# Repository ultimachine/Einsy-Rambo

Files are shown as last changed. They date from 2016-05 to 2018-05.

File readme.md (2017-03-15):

Mini-Rambo

3D Printer controller.

This board is based of RAMBo based off the Arduino MEGA design and work of RepRap community. It has 4 stepper drivers and 4 mosfet switched outputs.

There is no warantee for these files in any way. There may have been some undocumented tweaks by various designers, engineers, manufacturers, suppliers, and assemblers to make this a functional product.

#Version History
Note: This design was previously known as "Mini-RAMBo"  Previous versions of this design can be found at https://github.com/ultimachine/Mini-Rambo

v0.3a:
- Changed name from "Mini-Rambo" to "Einsy-Rambo".
- Uses the Trinamics TMC2130 motor driver in a 5x6mm QFN36 package.
- Added series resistance and TVS to selected signals.
- Overvoltage protection added to thermistors.
- Corrected and added testpoints
- Added GPIO connection "XTRA0" (currently unused) from 32U2, through the galvanic isolator, and into the Mega2560
- Added ferrite to AVdd pin of the 32U2
- Moved the XTAL of the 32U2
- Fixed the soldermask under the 5V buck regulator
- Removed via tenting underneath QFN packages, as well as all other packages with an SMT heat slug/tab
- Added pin1 marking to silkscreen
- Added teardrops to vias
- Changed via sizes to 10/22 and 15/30 (mils).
- Added GND polygon to XTAL of Mega2560
- Changes 5V inductor footprint for the 5V buck converter to fit two differing inductor package mechanicals
- Added I2C pullups (currently set to "Do Not Stuff")
- Adjustments to fuse holder footprint
- Decreased t-hole size of main power connector
- Fan connectors now have a third pin for reading fan tach pulses.
- Adjusted stackup to be more "standard"
- Added 100R to the gate of each FET

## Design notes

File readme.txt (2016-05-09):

Mini-Rambo readme

Part Changes
C40 0402 > 0603
C25 0603 > 0402
C49 0603 > 0402, 10nf > 1uF
F5 1210 > 1812
C1 0603 > 0402
C16 0603 > 0402

C30 change part to C1206C475K5PACTU - same values, worse tolerance, better supply chain, better price

Temporary use WSL2010R0600FEA18 for sense resistor on smps
Change R13 sense resistor to RL2512FK-070R06L

Proposed part changes
56R > 0R > REMOVED
0R > REMOVED

Extension connectors

Tasks
 Firmware
  Pins
  motor current by PWM
  
0.1 errata
PS_ON not connected 
LEDs placed 180 out
atmega2560, A4982 placed 270 out
PSMN70 placed offset in Y
USB fuse too close to USB connector. Remove?
No ESD path for USB, TVS diode added to bottom
No polarity indicator on connectors

0.2 errata
fuse holder hole too small, verify hole size is as spec'd
stencil sucks
No ESD path for USB, TVS diode added to bottom
 
Tests - Start up, Steady state, Transient states
EM
 voltage regulator
 motors
Temperatures
 Bed Fet
  V= 11 - 25, A= 15+
 Extruder Fet
  V= 11 - 25, A= 5+
 Fan Fets
 Motor Drivers
 Power traces
 Voltage regulator
ESD
 USB
Voltage
 Reverse voltage Input
 Min/Max voltage

Induced noise / interference
 ADC
 SMPS onto other lines
 
Stepper current circuit
 700mV P-P, ~40ns period. Saved #1 

Concerns
Fan connector selection.
Must be actively cooled.
motor output filters removed. necessity will need to be evalutated again for new design
see errata for individual versions above

Silk screen on QFN32
icsp typo

power from 5vsb leaves on with power off - jumper select

Fuse hole size

ATX testpoints 

clock too close to buzzer?

Change to smt connector? CNC tech has no button?

is clamping diode on motor power rail?

more pins broke out!!? 5v,tx,rx,gnd,reset  , i2c

tighten smps to allow shield

SMT extension headers? 

Shrink annular ring on usb 2x4

ATX
trace on D10 out jack

clean up polygons (bed)+
traces
silk screens

qfn and fets
no tent on vias
thermal pad print too small

ATX no option to force psu on with vcc set to 5V rail

1.0a //////////////////////////////////////////////////////////////////

add tp for vref & ? on top
xy e ref pins switched in firmware
label testpoints, bottom silk

1.1a////////////////////////////////////////////////
tent mosfet vias

1.3a errata
"Therm" silk screen too far right
T2 silk too far right.
via in F3 pads top right and bottom left
fuse hole size?

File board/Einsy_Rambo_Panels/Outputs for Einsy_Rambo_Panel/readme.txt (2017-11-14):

Readme File for Printed Circuit Board 'Einsy_Rambo_1.1a'

Board Specification
Part Number            Einsy_Rambo
Revision               1.1a
Board size             105 x 71mm
Board Thickness        1.524mm (0.06")
Board type             Rigid
Number of layers       6
P.C.B material         RoHS TG170
Finished Copper        2oz, 1oz (See Stackup)
Finish                 ENIG (Gold) (Lead free) (RoHS)
Mask type              See special requirement below
Mask color             Orange -See special requirement below
Silk screen color      Black -See special requirement below
Silk screen Sides      BOTH 
Min trace width        0.006"
Min clearance          0.008"
Min Hole Diameter >=   10mil
Gold Edge Connectors   No
Internal slots/routes  0
Blind Vias             No
Buried Vias            No
No of Boards/Panel     3
Routing                V-Score
Panel Size     116.8 X 226.1mm

Drill format           Leading zero suppression 2.4

Special Requirements
1. Fabricate PCB in accordiance with IPC-A-600 CLASS 2 (LATEST REVISION)
2. The PCB must be lead free assembly process compatible.
  Must handle minimum 6 cycles - 260C for 10 seconds.
3. Please ship panels including rails with tooling holes and fiducials in gerber files.
4.UL LOGO + ID and ROHS logo to be placed on solder side (bottom silk screen) by board fab in regions .
5. We wish to have an orange soldermask with a black soldermask on top. Print soldermask Orange as 
  provided. Print silk screen layer Einsy_Rambo_Panel.GTO INVERTED (negative) in black.
  The end result should be a black surface with orange silkscreen legend showing from beneath. 
  See image Black-Orange.png
6. Please note that extra top silkscreen has been poured around several QFN packages.
  Please do not remove this silkscreen... the silkscreen fixes an anomaly where black
  and orange soldermask stack up and raise the QFN package off of the land pattern.
  Placing the extra silckscreen causes the black soldermask to be removed in these areas,
  which fixes the problem.

Critical Tolerances: None

Layer Description
(Note: Inner layers are counted from the top downwards)
Top Paste                     Einsy_Rambo_Panel.GTP
Top Silk Screen               Einsy_Rambo_Panel.GTO
Top Solder Mask               Einsy_Rambo_Panel.GTS
Top Copper                    Einsy_Rambo_Panel.GTL
Inner Plane 1                 Einsy_Rambo_Panel.GP1
Inner Signal 1                Einsy_Rambo_Panel.G1
Inner Signal 2                Einsy_Rambo_Panel.G2
Inner Signal 3                Einsy_Rambo_Panel.G3
Bottom Copper                 Einsy_Rambo_Panel.GBL
Bottom Solder Mask            Einsy_Rambo_Panel.GBS
Bottom Silk Screen            Einsy_Rambo_Panel.GBO
NC Drill File                 Einsy_Rambo_Panel.TXT
Board Dimensions              Einsy_Rambo_Panel.GM8
Panel Dimensions              Einsy_Rambo_Panel.GM30
Panel                         Einsy_Rambo_Panel.GM1
Fabrication Notes             Einsy_Rambo_Panel.GM2
UL Logo Placement             Einsy_Rambo_Panel.GM29
Panel Dimension               Einsy_Rambo_Panel.GM30
V-Score                       Einsy_Rambo_Panel.GM31
Panel Outline                 Einsy_Rambo_Panel.GM32
IPC-D-356 Netlist             Einsy_Rambo_Panel IPC-D-356.net
Stackup                       Stack up.jpg

Contact Information
Address
Company        UltiMachine
Address        200 12th St. N.
City           South Pittsburg
State          TN
PostCode       37380
Country        USA
Email          info@ultimachine.com
Phone          423-228-0005

Purchasing contact:
Lee Turner - lee@ultimachine.com

Technical contacts:
Aaron Shepard - aaron@ultimachine.com 
Johnny Russell - johnny@ultimachine.com

Please quote quantities / lead time:
48 pieces = 16 panels - Rush
1002 pcs = 334 panels - 3 weeks
1002 pcs = 334 panels - 4 weeks
2004 pcs = 668 panels
4008 pcs = 1336 panels

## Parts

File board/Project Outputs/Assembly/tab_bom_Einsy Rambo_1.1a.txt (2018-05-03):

Comment	Description	Designator	Footprint	MANUFACTURER #	LibRef

"0R"	"RES SMD 0.0OHM JUMPER 1/10W 0402"	"RV24"	"R0402"	"ERJ-2GE0R00X"	"0R 0402"
"0R"	"RES SMD 0.0OHM JUMPER 1/10W 0603"	"R85"	"R0603"	"CR0603-J/-000ELF"	"0R 0603"
"0R0"	"RES 0.0 OHM 1/8W JUMP 0805 SMD"	"JP3, JP4"	"R0805"	"RMCF0805ZT0R00"	"0R0 1% 0805"
"0.22R"	"RES SMD 0.22 OHM 1% 1/3W 1206"	"R7, R10, R15, R17, R18, R22, R25, R26"	"R1206"	"RUT3216FR220CS"	"0.22R 1% 1206"
"0.6R"	"RES 0.06 OHM 1W 1% 2512 SMD"	"R13"	"2512R-0.55"	"RL2512FK-070R06L"	"RL2512FK-070R06L"
"1K"	"RES ARRAY 4 RES 1K 1206 62.5mW 5%"	"RN5"	"CAY16"	"CAY16-102J4LF"	"CAY16-102J4LF"
"1K"	"RES SMD 1K OHM 1% 1/16W 0402"	"R30, R33, R35, R44, R45, R69, R73, R79"	"R0402"	"RC0402FR-071KL"	"RC0402FR-071KL"
"1M"	"RES 0402 1M 100mW 5%"	"R72"	"R0402"	"ERJ2GEJ105X"	"ERJ2GEJ105X"
"1N4148WT"	"DIODE SOD523"	"D3, D4"	"SOD523"	"1N4148WT"	"1N4148WT"
"1nF"	"CAP CER 0603  1nF 50v 10% X7R"	"C65, C66, C75, C78, C80, C97, C98, C100, C101, C106, C107, C112, C114, C115, C117, C118"	"C0603"	"C0603C102K5RACTU"	"C0603C102K5RACTU"
"1uF"	"CAP CER 0402 1uF 6.3V 10% X5R"	"C126, C127, C128"	"C0402"	"GRM155R60J105KE19D"	"1uF 0402 6.3V X5R"
"1uF"	"CAP CER 0402 1uF 6.3V 10% X5R"	"C16, C61, C72, C76, C96"	"C0402"	"GRM155R60J105KE19D"	"GRM155R60J105KE19D"
"1uF"	"CAP CER 0805 1uF 50V 10% X7R"	"C35"	"C0805"	"GRM21BR71H105KA12L"	"GRM21BR71H105KA12L"
"1.8K"	"RES SMD 1.8K OHM 1% 1/16W 0402"	"R9, R16, R28, R29, R40, R58, R80"	"R0402"	"RC0402FR-071K8L"	"RC0402FR-071K8L"
"2-1437667-9"	"CONN BARRIER STRIP 6CIRC 0.325""	"J1"	"CON-Barrier-6-8.26mm"	"4DB-P108-06"	"2-1437667-9"
"2k37"	"RES SMD 2.37K OHM 1% 1/16W 0402"	"R6, R32, R37, R38, R39, R41, R53, R59, R63, R64, R81"	"R0402"	"RC0402FR-072K37L"	"RC0402FR-072K37L"
"2Mb"	"IC FLASH 2MBIT 104MHZ 8USON"	"U13"	"USON8 2X3"	"W25X20CLUXIG TR"	"W25X20CL"
"4.7k"	"RES SMD 4.7K OHM 1% 1/16W 0402"	"R5, R31, R36, R60, R65"	"R0402"	"RC0402FR-074K7L"	"RC0402FR-074K7L"
"4.7nF"	"CAP CER 0402 4.7nF 25V 10% X7R"	"C49, C63, C81"	"C0402"	"CC0402KRX7R8BB472"	"CC0402KRX7R8BB472"
"4.7uF"	"CAP CER 1206 4.7uF 50V 10% X5R"	"C30"	"C1206"	"C1206C475K5PACTU"	"C1206C475K5PACTU"
"7M-16.000MEEQ-T"	"Crystal 16mHz 10ppm 10pF"	"Y1, Y2"	"CRYS320250"	"7M-16.000MEEQ-T"	"7M-16.000MEEQ-T"
"10K"	"RES SMD 10K OHM 1% 1/16W 0402"	"R11, R23, R24, R46, R47, R51, R52, R54, R61, R62, R70, R71, R77, R78, R82"	"R0402"	"RC0402FR-0710KP"	"RC0402FR-0710KP"
"10K"	"RES SMD 10K OHM 1% 1/16W 0402"	"R55, R66, R68, R83, R84"	"R0402"	"RC0402FR-0710KP"	"10k 1% 0402"
"10R"	"RES SMD 10 OHM 1% 1/16W 0402"	"R4, R8, R12, R14"	"R0402"	"RC0402FR-0710RL"	"RC0402FR-0710RL"
"10uF"	"CAP CER 0805 10uF 10V 10% X5R"	"C2, C45"	"C0805"	"C0805C106K8PACTU"	"C0805C106K8PACTU"
"15uH"	"FIXED IND 15UH 2.5A 98 MOHM SMD"	"L1"	"XAL50xx_VLS6045"	"VLS6045EX-150M"	"IND 15uH 2.5A 0.075R"
"22nF"	"CAP CER 0402 22nF ±10% 50V X7R"	"C29, C34, C38, C91"	"C0402"	"GCM155R71H223KA55D"	"GCM155R71H223KA55D"
"22pF"	"CAP CER 0402 22pF 50V 5% C0G"	"C1, C12, C13, C57, C58"	"C0402"	"04025A220JAT2A"	"04025A220JAT2A"
"22R"	"RES 0402 22r 62.5mW 1%"	"R1, R2, R19, R20, R27, R34"	"R0402"	"RC0402FR-0722RL"	"RC0402FR-0722RL"
"74AHCT1G125"	"IC BUS BUFF TRI-ST N-INV  SOT-553"	"U9, U14"	"SOTFL50P160X60-5L"	"SN74AHCT1G125DRLR"	"SN74AHCT1G125DRLR"
"74LVC2G08"	"IC GATE AND 2CH 2-INP 8-VSSOP"	"U8"	"VSSOP8"	"74LVC2G08DC,125"	"74LVC2G08"
"100K"	"RES 100K OHM 1% 1/16W 0402"	"R43, R49, R50, R57"	"R0402"	"RC0402FR-07100KL"	"RC0402FR-07100KL"
"100K"	"RES SMD 100K OHM 1% 1/10W 0603"	"R87"	"R0603"	"ERJ-3EKF1003V"	"100k 1% 0603"
"100nF"	"CAP CER 0402 100nF 16V 10% X7R"	"C129, C130, C131"	"C0402"	"GRM155R71C104KA88D"	"100nF 0402 16V X7R"
"100nF"	"CAP CER 0402 100nF 16V 10% X7R"	"C4, C6, C7, C8, C9, C10, C11, C14, C15, C17, C26, C39, C41, C42, C43, C44, C46, C50, C51, C52, C53, C54, C55, C56, C59, C64, C67, C68, C69, C70, C73, C74, C77, C79, C83, C92, C94, C95, C120, C121, C122, C123, C124, C125"	"C0402"	"GRM155R71C104KA88D"	"GRM155R71C104KA88D"
"100nF"	"CAP CER 0603 100nF 50V 10% X7R"	"C3, C23, C25, C28, C31, C32, C33, C36, C37, C40, C60, C62, C71, C82, C84, C85, C86, C87, C88, C89, C90, C99, C102, C104, C105, C108, C110, C111, C113, C116, C119"	"C0603"	"C0603C104K5RACTU"	"C0603C104K5RACTU"
"100R"	"RES SMD 100 OHM 1% 1/16W 0402"	"R21, R42, R48, R56, R67, R74, R75, R76"	"R0402"	"RC0402FR-07100RL"	"RES 100R 0402 1%"
"120R"	"FERRITE BEAD 120 OHM 0402 1LN"	"FB24, FB25, FB26, FB27, FB28, FB29, FB30, FB31, FB32, FB33, FB34, FB35, FB36, FB37, RV8, RV18"	"R0402"	"BKP1005HS121-T"	"FERRITE 120R 1A 0402"
"120R"	"FERRITE BEAD 120 OHM 0603 1LN"	"FB3, FB4, FB5, FB6, FB7, FB8, FB9, FB10, FB11, FB12, FB13, FB14, FB15, FB16, FB17, FB18, FB19, FB20, FB21, FB22, FB23"	"FB0603"	"CIS10P121AC"	"FERRITE 120R 3A 0603"
"200K"	"RES 0402 200K"	"R3"	"R0402"	"CRCW0402200KFKED"	"CRCW0402200KFKED"
"0603"	"CAP CER 10UF 6.3V 10% JB 0603"	"C93"	"C0603"	"C1608JB0J106K080AB"	"C1608JB0J106K080AB"
"3557-2"	"FUSE PTH ATO"	"F1, F2, F3"	"3557"	"3557-2"	"3557-2"
"1571610-2"	"SWTCH Momentary Washable"	"S1"	"B3F-31XX"	"1571610-2"	"1571610-2"
"0395311002"	"Conn - 5.08mm Pitch Fixed"	"X13"	"MSTBV2"	"0395311002"	"0395311002"
"ADUM7441"	"4ch iCoupler"	"U10"	"QSOP16"	"ADUM7441ARQZ-RL7"	"ADUM7441"
"Atmega32u2"	"Atmega32u2"	"U1"	"QFN32_DualSolderMask"	"ATMEGA32U2-MUR"	"ATMEGA32U2-DualSolderMask"
"Atmega2560"	"Atmega2560"	"U2"	"TSQFP50P1600X1600X120-100L"	"ATMEGA2560-16AUR"	"ATMEGA2560AU_SM"
"BAT54"	"Diode Schottky 30V 100mA Surface Mount SOD-523"	"D1, D5, D11, D12, D13, D14, D15, D33, D34, D35, D36, D37"	"SOD523_IPC"	"BAT54WT-7"	"BAT54WT-7"
"BLM41PG600SN1L"	"FERRITE BEAD 1806 60ohm"	"FB1, FB2"	"L1806"	"BLM41PG600SN1L"	"BLM41PG600SN1L"
"CG0603MLC-05E"	"VAR 0603 5V"	"RV1, RV2, RV26"	"R0603"	"CG0603MLC-05E"	"CG0603MLC-05E"
"CONN 2PIN VERT 0.1" SHRD LOCKING"	"Connector 2pos"	"J2, J3, J6, J7, J13, J14, J16"	"70543-02"	"0705430001"	"CONN 2PIN VERT 0.1" SHRD LOCKING"
"FIDUCIAL"	"Fiducial"	"FID1, FID2, FID3"	"FIDUCIAL-1X2"	""	"FIDUCIAL"
"GRN"	"LED 0805 Green"	"LED7"	"LED2012120"	"5988170107F"	"5988170107F"
"HDR10"	"CONN HEADER VERT 10POS GOLD"	"P1, P2"	"HDR2X5 IDC"	"302-S101"	"Header 10PIN 2ROW T-HOLE VERT SHROUDED"
"HDR10"	"CONN HEADER VERT 10POS GOLD"	"P3"	"HDR2X5 IDC THIEVING"	"302-S101"	"Header 10PIN 2ROW T-HOLE VERT SHROUDED"
"HDR14"	"CONN RCPT DUAL ENTRY 14POS .100""	"J19"	"HDR2x7_SMT_BOT_ENTRY"	"969973-7"	"CONN 14PIN 0.1" FEMALE 2-ROW SMT BOT-ENTRY"
"LDO 3.3V 250mA"	"IC REG LINEAR 3.3V 250MA 4XDFN"	"U11"	"XDFN4 1X1"	"NCP160AMX330TBG"	"LDO 3.3V 250mA"
"LM25011MY/NOPB"	"REG BUCK"	"U3"	"VSSOP10_ClosedBotVias"	"LM25011MY/NOPB"	"LM25011_ClosedBotVias"
"MMBT3904"	"TRANS NPN 60V 0.2A SOT523"	"Q3"	"SOT523 SMALL"	"MMBT3904T-7-F"	"MMBT3904_SOT523"
"Molex 70543-03"	"3 Positions Header, Shrouded Connector 0.100" (2.54mm) Through Hole Gold"	"J4, J5"	"70543-03"	"0705430002"	"CONN 3POS VERT 0.1" SHRD LOCKING"
"Molex 0705430003"	"Molex 4 Pin Clip Connector"	"J8, J9, J10, J11, J12, J15"	"4POL254"	"0705430038"	"CONN 4PIN 0.1" VERT SHRD LOCK ALT"
"NCV8402AD"	"IC DVR LOW SIDE 8-SOIC"	"Q2"	"NCV8402AD-SOIC8"	"NCV8402ADDR2G"	"NCV8402AD"
"NTCG104LH104JT1"	"Resistor"	"RT1"	"R0402"	""	"R0402TBD"
"PINHD-2X3"	"CONN HEADER VERT 6POS GOLD"	"X17"	"2X03"	"2213S-06G"	"PINHD-2X3"
"PSMN1R8-40YLC,115"	"MOSFET N-CH 40V 100A LFPAK"	"Q1, Q5"	"SOT669_ClosedBotVias"	"PSMN1R8-40YLC,115"	"PSMN1R8-40YLC_ClosedBotVias"
"R0603TBD"	"Resistor"	"R86"	"R0603"	""	"R0603TBD"
"RED"	"LED 0805 Red"	"LED2, LED3, LED5, LED6"	"LED2012120"	"5988110107F"	"5988110107F"
"RJ-45"	"CONN MOD JACK 8P8C R/A SHIELDED"	"P4"	""	"RJCSE538001"	"RJ45 SMT"
"RSB39VTE-17"	"DIODE TVS"	"D16"	"SOD323-R"	"RSB39VTE-17"	"RSB39VTE-17"
"S3A-13-F"	"DIODE DO-214AB"	"D7"	"DO-214AB"	"S3A-13-F"	"S3A-13-F"
"SK310A-TP"	"DIODE Schottky 3A SMA"	"D6, D9, D10"	"SMA-SM"	"SK310A-LTP"	"SK310A"
"SMAJ28A"	"TVS DIODE 28VWM 45.4VC SMA"	"D2, D8"	"SMA-SM"	"SMAJ28A-13-F"	"SMAJ28A"
"SN74LVC125A"	"IC BUS BUFF TRI-ST QD 14VQFN"	"U12"	"PVQFN14_3.5X3.5"	"SN74LVC125ARGYR"	"SN74LVC125A"
"TMC2130-LA"	"IC STEPPER MOTOR DVR SPI 36QFN"	"U4, U5, U6, U7"	"QFN36-DualSolderMask"	"TMC2130-LA-T"	"TMC2130-DualSolderMask"
"USB-B"	"USB connector B PTH"	"X2"	"PN61729"	"61729-0010BLF"	"USB-B"
"UWT1V101MCL1GS"	"CAP ALUM 100UF 35V 20% SMD"	"C5, C18, C24, C27, C103, C109"	"CAP-ELEC-063063077"	"UWT1V101MCL1GS"	"UWT1V101MCL1GS"
"VRS0402SR55R101N"	"Multi-Layer Varistor"	"RV3, RV5, RV7, RV27"	"C0402"	"VRS0402SR55R101N"	"VRS0402SR55R101N"
"YEL"	"LED 0805 Yellow"	"LED1, LED4, LED10"	"LED2012120"	"5988140107F"	"5988140107F"

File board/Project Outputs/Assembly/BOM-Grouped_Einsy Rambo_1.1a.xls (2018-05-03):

Designator | DISTRIBUTOR | DISTRIBUTOR # | Manufacturer | MANUFACTURER # | PART | Quantity | DNI | Comment | Footprint | Description | Part Description | VALUE | Tolerance | EE_SPEC
C1, C12, C13, C57, C58 | Digi-Key | 478-1074-2-ND | AVX | 04025A220JAT2A | 22pF 50V | 5.0 |  | 22pF | C0402 | CAP CER 0402 22pF 50V 5% C0G | 22pF ±5% 50V Ceramic Capacitor C0G, NP0 0402 (1005 Metric) | 22pF | 5% | 22pF 5% 50V NP0 0402
C2, C45 | Digi-Key | 399-4925-2-ND | Kemet | C0805C106K8PACTU | 10uF | 2.0 |  | 10uF | C0805 | CAP CER 0805 10uF 10V 10% X5R | 10µF ±10% 10V Ceramic Capacitor X5R 0805 (2012 Metric) | 10uF | +/- 10% | 10uF 10V X5R 0805
C3, C23, C25, C28, C31, C32, C33, C36, C37, C40, C60, C62, C71, C82, C84, C85, C86, C87, C88, C89, C90, C99, C102, C104, C105, C108, C110, C111, C113, C116, C119 | Digi-Key | 399-5089-2-ND | Kemet | C0603C104K5RACTU | 100nF | 31.0 |  | 100nF | C0603 | CAP CER 0603 100nF 50V 10% X7R | 0.1µF ±10% 50V Ceramic Capacitor X7R 0603 (1608 Metric) | 100nF | +/- 10% | 100nF 50V X7R 0603
C4, C6, C7, C8, C9, C10, C11, C14, C15, C17, C26, C39, C41, C42, C43, C44, C46, C50, C51, C52, C53, C54, C55, C56, C59, C64, C67, C68, C69, C70, C73, C74, C77, C79, C83, C92, C94, C95, C120, C121, C122, C123, C124, C125, C129, C130, C131 | Digi-Key, Digi-Key, Digi-Key, Digi-Key, Digi-Key, Digi-Key, Digi-Key, Digi-Key, Digi-Key, Digi-Key, Digi-Key, Digi-Key, Digi-Key, Digi-Key, Digi-Key, Digi-Key, Digi-Key, Digi-Key, Digi-Key, Digi-Key, Digi-Key, Digi-Key, Digi-Key, Digi-Key, Digi-Key, Digi-Key, Digi-Key, Digi-Key, Digi-Key, Digi-Key, Digi-Key, Digi-Key, Digi-Key, Digi-Key, Digi-Key, Digi-Key, Digi-Key, Digi-Key, Digi-Key, Digi-Key, Digi-Key, Digi-Key, Digi-Key, Digi-Key, Digikey, Digikey, Digikey | 490-3261-2-ND | Murata | GRM155R71C104KA88D | 100nF, 100nF, 100nF, 100nF, 100nF, 100nF, 100nF, 100nF, 100nF, 100nF, 100nF, 100nF, 100nF, 100nF, 100nF, 100nF, 100nF, 100nF, 100nF, 100nF, 100nF, 100nF, 100nF, 100nF, 100nF, 100nF, 100nF, 100nF, 100nF, 100nF, 100nF, 100nF, 100nF, 100nF, 100nF, 100nF, 100nF, 100nF, 100nF, 100nF, 100nF, 100nF, 100nF, 100nF, 0.1uF 16V X7R 0402, 0.1uF 16V X7R 0402, 0.1uF 16V X7R 0402 | 47.0 |  | 100nF | C0402 | CAP CER 0402 100nF 16V 10% X7R | 0.10µF ±10% 16V Ceramic Capacitor X7R 0402 (1005 Metric) | 100nF | +/- 10%, +/- 10%, +/- 10%, +/- 10%, +/- 10%, +/- 10%, +/- 10%, +/- 10%, +/- 10%, +/- 10%, +/- 10%, +/- 10%, +/- 10%, +/- 10%, +/- 10%, +/- 10%, +/- 10%, +/- 10%, +/- 10%, +/- 10%, +/- 10%, +/- 10%, +/- 10%, +/- 10%, +/- 10%, +/- 10%, +/- 10%, +/- 10%, +/- 10%, +/- 10%, +/- 10%, +/- 10%, +/- 10%, +/- 10%, +/- 10%, +/- 10%, +/- 10%, +/- 10%, +/- 10%, +/- 10%, +/- 10%, +/- 10%, +/- 10%, +/- 10%, 10%, 10%, 10% | 100nF 16V X7R 0402, 100nF 16V X7R 0402, 100nF 16V X7R 0402, 100nF 16V X7R 0402, 100nF 16V X7R 0402, 100nF 16V X7R 0402, 100nF 16V X7R 0402, 100nF 16V X7R 0402, 100nF 16V X7R 0402, 100nF 16V X7R 0402, 100nF 16V X7R 0402, 100nF 16V X7R 0402, 100nF 16V X7R 0402, 100nF 16V X7R 0402, 100nF 16V X7R 0402, 100nF 16V X7R 0402, 100nF 16V X7R 0402, 100nF 16V X7R 0402, 100nF 16V X7R 0402, 100nF 16V X7R 0402, 100nF 16V X7R 0402, 100nF 16V X7R 0402, 100nF 16V X7R 0402, 100nF 16V X7R 0402, 100nF 16V X7R 0402, 100nF 16V X7R 0402, 100nF 16V X7R 0402, 100nF 16V X7R 0402, 100nF 16V X7R 0402, 100nF 16V X7R 0402, 100nF 16V X7R 0402, 100nF 16V X7R 0402, 100nF 16V X7R 0402, 100nF 16V X7R 0402, 100nF 16V X7R 0402, 100nF 16V X7R 0402, 100nF 16V X7R 0402, 100nF 16V X7R 0402, 100nF 16V X7R 0402, 100nF 16V X7R 0402, 100nF 16V X7R 0402, 100nF 16V X7R 0402, 100nF 16V X7R 0402, 100nF 16V X7R 0402, 16V, 16V, 16V
C5, C18, C24, C27, C103, C109 | Digi-Key | 493-2203-2-ND | Nichicon | UWT1V101MCL1GS | 100uF | 6.0 |  | UWT1V101MCL1GS | CAP-ELEC-063063077 | CAP ALUM 100UF 35V 20% SMD | 100µF 35V Aluminum Capacitors Radial, Can - SMD 1000 Hrs @ 105°C | 100uF | +/- 20% | 100uF 35V Al-El
C16, C61, C72, C76, C96, C126, C127, C128 | Digi-Key, Digi-Key, Digi-Key, Digi-Key, Digi-Key, Digikey, Digikey, Digikey | 490-1320-2-ND | Murata | GRM155R60J105KE19D | 1uF, 1uF, 1uF, 1uF, 1uF, 1uF 6.3V X5R 0402, 1uF 6.3V X5R 0402, 1uF 6.3V X5R 0402 | 8.0 |  | 1uF | C0402 | CAP CER 0402 1uF 6.3V 10% X5R | 1µF ±10% 6.3V Ceramic Capacitor X5R 0402 (1005 Metric) | 1uF | +/- 10%, +/- 10%, +/- 10%, +/- 10%, +/- 10%, 10%, 10%, 10% | 1uF 6.3V X5R 0402, 1uF 6.3V X5R 0402, 1uF 6.3V X5R 0402, 1uF 6.3V X5R 0402, 1uF 6.3V X5R 0402, 6.3V, 6.3V, 6.3V
C29, C34, C38, C91 | Digi-Key | 490-4763-2-ND | YAGEO | GCM155R71H223KA55D | 22nF | 4.0 |  | 22nF | C0402 | CAP CER 0402 22nF ±10% 50V X7R | 0.022µF ±10% 50V Ceramic Capacitor X7R 0402 (1005 Metric) | 22nF | +/- 10% | 22nF 50V X7R 0402
C30 | Digi-Key | 399-5507-2-ND | Kemet | C1206C475K5PACTU | 4.7uF | 1.0 |  | 4.7uF | C1206 | CAP CER 1206 4.7uF 50V 10% X5R | 4.7µF ±10% 50V Ceramic Capacitor X5R 1206 (3216 Metric) | 4.7uF | +/- 10% | 4.7uF 50V X5R 1206
C35 | Digi-Key | 490-4736-2-ND | Murata | GRM21BR71H105KA12L | 1uF | 1.0 |  | 1uF | C0805 | CAP CER 0805 1uF 50V 10% X7R | 1µF ±10% 50V Ceramic Capacitor X7R 0805 (2012 Metric) | 1uF | +/- 10% | 1uF 50V X7R 0805
C49, C63, C81 | Digi-Key | 311-1039-2-ND | YAGEO | CC0402KRX7R8BB472 | 4.7nF | 3.0 |  | 4.7nF | C0402 | CAP CER 0402 4.7nF 25V 10% X7R | 4700pF ±10% 25V Ceramic Capacitor X7R 0402 (1005 Metric) | 4.7nF | +/- 10% | 4.7nF 25V X7R 0402
C65, C66, C75, C78, C80, C97, C98, C100, C101, C106, C107, C112, C114, C115, C117, C118 | Digi-Key | 399-1082-2-ND | Kemet | C0603C102K5RACTU | 1nF | 16.0 |  | 1nF | C0603 | CAP CER 0603 1nF 50v 10% X7R | 1000pF ±10% 50V Ceramic Capacitor X7R 0603 (1608 Metric) | 1nF | +/- 10% | 1nF 50V X7R 0603
C93 | Digi-Key | 445-11185-1-ND | TDK | C1608JB0J106K080AB | 10uF 6.3VDC | 1.0 |  | 0603 | C0603 | CAP CER 10UF 6.3V 10% JB 0603 | CAP CER 10UF 6.3V 10% JB 0603 | 10uF 6.3VDC | +/- 10% | 6.3VDC
D1, D5, D11, D12, D13, D14, D15, D33, D34, D35, D36, D37 | Digi-Key | BAT54WT-7DI-ND | Diodes Incorporated | BAT54WT-7 | BAT54 | 12.0 |  | BAT54 | SOD523_IPC | Diode Schottky 30V 100mA Surface Mount SOD-523 | Diode Schottky 30V 100mA Surface Mount SOD-523 | BAT54 | NA | 30V 0.1A
D2, D8 | Digi-Key | SMAJ28A-FDITR-ND | Diodes Inc | SMAJ28A-13-F | SMAJ28A | 2.0 |  | SMAJ28A | SMA-SM | TVS DIODE 28VWM 45.4VC SMA | TVS DIODE 28VWM 45.4VC SMA | SMAJ28A | NA | 28Vrs 45.4Vc
D3, D4 | Digi-Key | 1N4148WTTR-ND | Fairchild | 1N4148WT | 1N4148WT | 2.0 |  | 1N4148WT | SOD523 | DIODE SOD523 | DIODE GEN PURP 75V 200MA SOD523F | 1N4148WT | NA | 75V 0.2A
D6, D9, D10 | Digi-Key | SK310A-LTPMSTR-ND | MCC | SK310A-LTP | SK310A | 3.0 |  | SK310A-TP | SMA-SM | DIODE Schottky 3A SMA | Diode Schottky 100V 3A Surface Mount DO-214AC (SMA) | SK310A | NA | 3A 100V
D7 | Digi-Key | S3A-FDITR-ND | Diodes Incorporated | S3A-13-F | S3A-13-F | 1.0 |  | S3A-13-F | DO-214AB | DIODE DO-214AB | Diode Standard 50V 3A Surface Mount SMC | S3A-13-F | NA | 50V 3A 1.15Vf
D16 | Digi-Key | RSB39VTE-17TR-ND | Rohm | RSB39VTE-17 | 30V | 1.0 |  | RSB39VTE-17 | SOD323-R | DIODE TVS | TVS DIODE 30VWM SOD323 | 30V | NA | 30Vrs 35.1Vbd 30pF
F1, F2, F3 | Digi-Key | 36-3557-2-ND | Keystone | 3557-2 | Fuse | 3.0 |  | 3557-2 | 3557 | FUSE PTH ATO | FUSE BLOCK BLADE 500V 30A PCB | Fuse | NA | ATC 500V 30A
FB1, FB2 | Digi-Key | 490-1058-2-ND | Murata | BLM41PG600SN1L | 60Rf | 2.0 |  | BLM41PG600SN1L | L1806 | FERRITE BEAD 1806 60ohm | FERRITE BEAD 60 OHM 1806 1LN | 60R | NA | 60R 6A 0.009Ohm
FB3, FB4, FB5, FB6, FB7, FB8, FB9, FB10, FB11, FB12, FB13, FB14, FB15, FB16, FB17, FB18, FB19, FB20, FB21, FB22, FB23 | DigiKey | 1276-6351-2-ND | Samsung | CIS10P121AC | FERRITE 120R 3A 0603 | 21.0 |  | 120R | FB0603 | FERRITE BEAD 120 OHM 0603 1LN | FERRITE BEAD 120 OHM 0603 1LN | 120Rfb | -NA- | 3A
FB24, FB25, FB26, FB27, FB28, FB29, FB30, FB31, FB32, FB33, FB34, FB35, FB36, FB37, RV8, RV18 | Digikey | 587-1921-2-ND | Taiyo Yuden | BKP1005HS121-T | FERRITE 120R 1A 0402 | 16.0 |  | 120R | R0402 | FERRITE BEAD 120 OHM 0402 1LN | FERRITE BEAD 120 OHM 0402 1LN | 120Rfb | -NA- | 1A
FID1, FID2, FID3, R86, RT1 |  |  |  |  |  | 5.0 |  | FIDUCIAL, FIDUCIAL, FIDUCIAL, R0603TBD, NTCG104LH104JT1 | FIDUCIAL-1X2, FIDUCIAL-1X2, FIDUCIAL-1X2, R0603, R0402 | Fiducial, Fiducial, Fiducial, Resistor, Resistor |  | [NoValue], [NoValue], [NoValue], R0603TBD, NTCG104LH104JT1
J1 | Digi-Key | A98476-ND | TE | 4DB-P108-06 | 6POS | 1.0 |  | 2-1437667-9 | CON-Barrier-6-8.26mm | CONN BARRIER STRIP 6CIRC 0.325" | 6 Circuit 0.325" (8.26mm) Barrier Block Connector, Screws with Captive Plate | 6POS | NA | 150V 2A
J2, J3, J6, J7, J13, J14, J16 | Digi-Key | WM4800-ND | Molex | 0705430001 | 10 Pin Conn | 7.0 |  | CONN 2PIN VERT 0.1" SHRD LOCKING | 70543-02 | Connector 2pos | 2 Positions Header, Shrouded Connector 0.100" (2.54mm) Through Hole Gold | HDR2 | -NA- | -NA-
J4, J5 | Digi-Key | WM4801-ND | Molex | 0705430002 | 3 Pin Conn VERT | 2.0 |  | Molex 70543-03 | 70543-03 | 3 Positions Header, Shrouded Connector 0.100" (2.54mm) Through Hole Gold | 3 Positions Header, Shrouded Connector 0.100" (2.54mm) Through Hole Gold | HDR3 | -NA- | -NA-
J8, J9, J10, J11, J12, J15 | Digi-Key | WM4826-ND | Molex | 0705430038 | 4 Pin Conn | 6.0 |  | Molex 0705430003 | 4POL254 | Molex 4 Pin Clip Connector | 4 Positions Header, Shrouded Connector 0.100" (2.54mm) Through Hole Tin | HDR4 | -NA- | -NA-
J19 | Digikey | A107060CT-ND | TE Connectivity | 969973-7 | HDR14 | 1.0 |  | HDR14 | HDR2x7_SMT_BOT_ENTRY | CONN RCPT DUAL ENTRY 14POS .100" | 14 Position Receptacle, Bottom or Top Entry Connector Gold 0.100" (2.54mm) Surface Mount | HDR14 | -NA- | -NA-
JP3, JP4 | Digi-Key | RMCF0805ZT0R00CT-ND | STACKPOLE | RMCF0805ZT0R00 | 0R0 | 2.0 |  | 0R0 | R0805 | RES 0.0 OHM 1/8W JUMP 0805 SMD | 0 Ohms Jumper 0.125W, 1/8W Chip Resistor 0805 (2012 Metric) Automotive AEC-Q200 Thick Film | 0R0 | 1% | 0.125W
L1 | Digi-Key | 445-173041-2-ND | TDK | VLS6045EX-150M | 15uH | 1.0 |  | 15uH | XAL50xx_VLS6045 | FIXED IND 15UH 2.5A 98 MOHM SMD | 15µH Shielded Wirewound Inductor 2.5A 98 mOhm Max Nonstandard | 15uH | +/- 20% | 15uH 2.5A 0.098-Ohm
LED1, LED4, LED10 | Digi-Key | 350-2041-2-ND | Dialight | 5988140107F | YEL | 3.0 |  | YEL | LED2012120 | LED 0805 Yellow | Yellow 593nm LED Indication - Discrete 2V 0805 (2012 Metric) | YEL | NA | 2V 0.02A
LED2, LED3, LED5, LED6 | Digi-Key | 350-2038-2-ND | Dialight | 5988110107F | RED | 4.0 |  | RED | LED2012120 | LED 0805 Red | Red 635nm LED Indication - Discrete 2.2V 0805 (2012 Metric) | RED | NA | 2.2V 0.02A
LED7 | Digi-Key | 350-2044-2-ND | Dialight | 5988170107F | GRN | 1.0 |  | GRN | LED2012120 | LED 0805 Green | Green 566nm LED Indication - Discrete 2V 0805 (2012 Metric) | GRN | NA | 2V 0.02A
P1, P2, P3 | Digikey | ED1543-ND | On Shore | 302-S101 | HDR10 | 3.0 |  | HDR10 | HDR2X5 IDC, HDR2X5 IDC, HDR2X5 IDC THIEVING | CONN HEADER VERT 10POS GOLD | 10 Positions Header Connector 0.100" (2.54mm) Through Hole Gold | HDR10 | -NA- | -NA-
P4 | Digikey | RJCSE538001TR-ND | Amphenol | RJCSE538001 | RJ-45 | 1.0 |  | RJ-45 |  | CONN MOD JACK 8P8C R/A SHIELDED | Jack Modular Connector 8p8c (RJ45, Ethernet) 90° Angle (Right) Shielded, EMI Finger |  | NA
Q1, Q5 | Digikey | 1727-1052-2-ND | Nexperia | PSMN1R8-40YLC,115 |  | 2.0 |  | PSMN1R8-40YLC,115 | SOT669_ClosedBotVias | MOSFET N-CH 40V 100A LFPAK | N-Channel 40V 100A (Tc) 272W (Tc) Surface Mount LFPAK56, Power-SO8 | N-FET | -NA- | 40V 100A 1.8mOhm
Q2 | Digi-Key | NCV8402ADDR2GOSTR-ND | On Semi | NCV8402ADDR2G | NCV8402 | 1.0 |  | NCV8402AD | NCV8402AD-SOIC8 | IC DVR LOW SIDE 8-SOIC | IC DVR LOW SIDE 8-SOIC | NCV8402 | NA | 42Vmaz 2A 0.165-Ohm
Q3 | Digikey | MMBT3904T-FDITR-ND | Diodes Incorporated | MMBT3904T-7-F | TRANS NPN 40V 0.2A SOT523 | 1.0 |  | MMBT3904 | SOT523 SMALL | TRANS NPN 60V 0.2A SOT523 | Bipolar (BJT) Transistor NPN 40V 200mA 300MHz 150mW Surface Mount SOT-523 | NPN | -NA- | 40V 0.2A
R1, R2, R19, R20, R27, R34 | Digi-Key | 311-22.0LRTR-ND | Yageo | RC0402FR-0722RL | 22R | 6.0 |  | 22R | R0402 | RES 0402 22r 62.5mW 1% | 22 Ohm ±1% 0.063W, 1/16W Chip Resistor 0402 (1005 Metric) Moisture Resistant Thick Film | 22R | +/- 1% | 22R 1% 0402
R3 | Digi-Key | 541-200KLTR-ND | Vishay Dale | CRCW0402200KFKED | 200K | 1.0 |  | 200K | R0402 | RES 0402 200K | 200k Ohm ±1% 0.063W, 1/16W Chip Resistor 0402 (1005 Metric) Automotive AEC-Q200 Thick Film | 200K | +/- 1% | 200k 1% 0402
R4, R8, R12, R14 | Digi-Key | 311-10.0LRTR-ND | Yageo | RC0402FR-0710RL | 10R | 4.0 |  | 10R | R0402 | RES SMD 10 OHM 1% 1/16W 0402 | 10 Ohm ±1% 0.063W, 1/16W Chip Resistor 0402 (1005 Metric) Moisture Resistant Thick Film | 10R | +/- 1% | 10R 1% 0402
R5, R31, R36, R60, R65 | Digi-Key | 311-4.7KLRTR-ND | Yageo | RC0402FR-074K7L | 4.7k | 5.0 |  | 4.7k | R0402 | RES SMD 4.7K OHM 1% 1/16W 0402 | 4.7k Ohm ±1% 0.063W, 1/16W Chip Resistor 0402 (1005 Metric) Moisture Resistant Thick Film | 4.7k | +/- 1% | 4.7k 1% 0402
R6, R32, R37, R38, R39, R41, R53, R59, R63, R64, R81 | Digi-Key | 311-2.37KLRTR-ND | Yageo | RC0402FR-072K37L | 2.37k | 11.0 |  | 2k37 | R0402 | RES SMD 2.37K OHM 1% 1/16W 0402 | 2.37k Ohm ±1% 0.063W, 1/16W Chip Resistor 0402 (1005 Metric) Moisture Resistant Thick Film | 2k37 | +/- 1% | 2.37k 1% 0402
R7, R10, R15, R17, R18, R22, R25, R26 | Digi-Key | RUT3216FR220CS | Panasonic | RUT3216FR220CS | 0.22R | 8.0 |  | 0.22R | R1206 | RES SMD 0.22 OHM 1% 1/3W 1206 | RES SMD 0.22 OHM 1% 1/3W 1206 | 0.22R | +/- 1% | 0.22R 1% 1206
R9, R16, R28, R29, R40, R58, R80 | Digi-Key | 311-1.80KLRTR-ND | Yageo | RC0402FR-071K8L | 1.8k | 7.0 |  | 1.8K | R0402 | RES SMD 1.8K OHM 1% 1/16W 0402 | 1.8k Ohm ±1% 0.063W, 1/16W Chip Resistor 0402 (1005 Metric) Moisture Resistant Thick Film | 1.8K | +/- 1% | 1.8k 1% 0402
R11, R23, R24, R46, R47, R52, R54, R55, R62, R66, R68, R70, R71, R77, R78, R82, R83, R84 | Digi-Key, Digi-Key, Digi-Key, Digi-Key, Digi-Key, Digi-Key, Digi-Key, Digi-key, Digi-Key, Digi-key, Digi-key, Digi-Key, Digi-Key, Digi-Key, Digi-Key, Digi-Key, Digikey, Digi-key | YAG1249TR-ND | Yageo | RC0402FR-0710KP | 10k 1% 0402 | 18.0 |  | 10K | R0402 | RES SMD 10K OHM 1% 1/16W 0402 | 10k Ohm ±1% 0.063W, 1/16W Chip Resistor 0402 (1005 Metric) Moisture Resistant Thick Film | 10K | 1% | 10k 1% 0402 1/16W, 10k 1% 0402 1/16W, 10k 1% 0402 1/16W, 10k 1% 0402 1/16W, 10k 1% 0402 1/16W, 10k 1% 0402 1/16W, 10k 1% 0402 1/16W, 10k 1% 0402 1/16W, 10k 1% 0402 1/16W, 10k 1% 0402 1/16W, 10k 1% 0402 1/16W, 10k 1% 0402 1/16W, 10k 1% 0402 1/16W, 10k 1% 0402 1/16W, 10k 1% 0402 1/16W, 10k 1% 0402 1/16W, 1/16W, 10k 1% 0402 1/16W
R13 | Digi-Key | 311-0.06TTR-ND | Yageo | RL2512FK-070R06L | 0.6R | 1.0 |  | 0.6R | 2512R-0.55 | RES 0.06 OHM 1W 1% 2512 SMD | 0.06 Ohm ±1% 1W Chip Resistor 2512 (6432 Metric) Automotive AEC-Q200, Current Sense, Moisture Resistant Thick Film | 0.6R | 1% | 0.06R 1% 2512
R21, R42, R48, R56, R67, R74, R75, R76 | Digi-Key | 311-100LRTR-ND | Yageo | RC0402FR-07100RL | 100R 1% 0402 | 8.0 |  | 100R | R0402 | RES SMD 100 OHM 1% 1/16W 0402 | 100 Ohm ±1% 0.063W, 1/16W Chip Resistor 0402 (1005 Metric) Moisture Resistant Thick Film | 100R | 1% | 100R 1% 0402
R30, R33, R35, R44, R45, R69, R73, R79 | Digi-Key | 311-1.00KLRTR-ND | Yageo | RC0402FR-071KL | 1k | 8.0 |  | 1K | R0402 | RES SMD 1K OHM 1% 1/16W 0402 | 1k Ohm ±1% 0.063W, 1/16W Chip Resistor 0402 (1005 Metric) Moisture Resistant Thick Film | 1K | +/- 1% | 1k 1% 0402
R43, R49, R50, R57 | Digi-Key | 311-100KLRTR-ND | Yageo | RC0402FR-07100KL | 100K | 4.0 |  | 100K | R0402 | RES 100K OHM 1% 1/16W 0402 | 100k Ohm ±1% 0.063W, 1/16W Chip Resistor 0402 (1005 Metric) Moisture Resistant Thick Film | 100K | +/- 1% | 100K 1% 0402
R51, R61 | Digi-Key | YAG1249TR-ND | Yageo | RC0402FR-0710KP | 10k 1% 0402 | 2.0 | DNI | 10K | R0402 | RES SMD 10K OHM 1% 1/16W 0402 | 10k Ohm ±1% 0.063W, 1/16W Chip Resistor 0402 (1005 Metric) Moisture Resistant Thick Film | 10K | 1% | 10k 1% 0402 1/16W
R72 | Digi-Key | P1.0MJTR-ND | Panasonic | ERJ2GEJ105X | 1M | 1.0 |  | 1M | R0402 | RES 0402 1M 100mW 5% | 1M Ohm ±5% 0.1W, 1/10W Chip Resistor 0402 (1005 Metric) Automotive AEC-Q200 Thick Film | 1M | +/- 1% | 1M 1% 0402
R85 | Digikey | CR0603-J/-000ELFTR-ND | Bourns | CR0603-J/-000ELF | 0R | 1.0 |  | 0R | R0603 | RES SMD 0.0OHM JUMPER 1/10W 0603 | 0.0 Ohm Jumper 0.1W, 1/10W Chip Resistor 0603 (1608 Metric) Moisture Resistant Thick Film | 0R | -NA- | 0R 0603
R87 | Digikey | P100KHTR-ND | Panasonic | ERJ-3EKF1003V | 100k 1% 0603 | 1.0 |  | 100K | R0603 | RES SMD 100K OHM 1% 1/10W 0603 | 100 kOhms ±1% 0.1W, 1/10W Chip Resistor 0603 (1608 Metric) Automotive AEC-Q200 Thick Film | 100K | 1% | 1/10W
RN5 | Digi-Key | CAY16-102J4LFTR-ND | Bourns | CAY16-102J4LF | 1K | 1.0 |  | 1K | CAY16 | RES ARRAY 4 RES 1K 1206 62.5mW 5% | 1k Ohm ±5% 62.5mW Power Per Element Isolated Resistor Network/Array ±200ppm/°C 1206 (3216 Metric), Convex, Long Side Terminals | 1K | +/- 5% | 1k 5% Array_x_4
RV1, RV2, RV26 | Digi-Key | CG0603MLC-05ETR-ND | YAGEO | CG0603MLC-05E | 5VDC | 3.0 |  | CG0603MLC-05E | R0603 | VAR 0603 5V | VARISTOR 0603 | 5V | NA | 5VDC
RV3, RV5, RV7, RV27 | Digi-Key | 311-1516-2-ND | Yageo | VRS0402SR55R101N | 12V | 4.0 |  | VRS0402SR55R101N | C0402 | Multi-Layer Varistor | VARISTOR 12V 10A 0402 | 12V | NA | 5.5Vdc 12Vvar 60pF
RV24 | Digikey | P0.0JTR-ND | Panasonic | ERJ-2GE0R00X | 0R | 1.0 |  | 0R | R0402 | RES SMD 0.0OHM JUMPER 1/10W 0402 | 0.0 Ohm Jumper 0.1W, 1/10W Chip Resistor 0402 (1005 Metric) Automotive AEC-Q200 Thick Film | 0R | 1%
S1 | Digi-Key | 506-1571610-2 | TE | 1571610-2 | Tact PB R/A | 1.0 |  | 1571610-2 | B3F-31XX | SWTCH Momentary Washable | Tactile Switches R/A SEALED TACT SWITCH | Tact PB R/A | NA | 24V 0.05A
U1 | Digi-Key | ATMEGA32U2-MURTR-ND | Microchip | ATMEGA32U2-MUR | ATMEGA32U2 | 1.0 |  | Atmega32u2 | QFN32_DualSolderMask | Atmega32u2 | AVR AVR® ATmega Microcontroller IC 8-Bit 16MHz 32KB (16K x 16) FLASH 32-VQFN (5x5) | ATMEGA32U2 | NA | 5V 32KB 1KB
U2 | Digi-Key | ATMEGA2560-16AURTR-ND | Microchip | ATMEGA2560-16AUR | ATMEGA2560 | 1.0 |  | Atmega2560 | TSQFP50P1600X1600X120-100L | Atmega2560 | AVR AVR® ATmega Microcontroller IC 8-Bit 16MHz 256KB (128K x 16) FLASH 100-TQFP (14x14) | ATMEGA2560 | NA | 5V 256KB 8KB 16MHz
U3 | Digikey | LM25011MY/NOPBTR-ND | Texas Instruments | LM25011MY/NOPB | IC VREG BUCK ADJ 2A 10MSOP | 1.0 |  | LM25011MY/NOPB | VSSOP10_ClosedBotVias | REG BUCK | Buck Switching Regulator IC Positive Adjustable 2.51V 1 Output 2A 10-TFSOP, 10-MSOP (0.118", 3.00mm Width) Exposed Pad | LM25011MY/NOPB | -NA- | 2A 42Vin_max
U4, U5, U6, U7 | Digi-Key | 1460-1130-2-ND | Trinamic | TMC2130-LA-T | TMC2130 | 4.0 |  | TMC2130-LA | QFN36-DualSolderMask | IC STEPPER MOTOR DVR SPI 36QFN | Bipolar Motor Driver Power MOSFET SPI, Step/Direction 36-QFN (5x6) | TMC2130 | NA | 46V 1.2A 1/256 Step
U8 | Digikey | 1727-3560-2-ND | Nexperia | 74LVC2G08DC,125 | 74LVC2G08 | 1.0 |  | 74LVC2G08 | VSSOP8 | IC GATE AND 2CH 2-INP 8-VSSOP | AND Gate IC 2 Channel 8-VSSOP, US8 | -NA- | -NA- | 1.65-5.5V, 32mA, LVTTL
U9, U14 | Digikey | 296-19379-2-ND | TI | SN74AHCT1G125DRLR | SN74AHCT1G125DRLR | 2.0 |  | 74AHCT1G125 | SOTFL50P160X60-5L | IC BUS BUFF TRI-ST N-INV SOT-553 | Buffer, Non-Inverting 1 Element 1 Bit per Element Push-Pull Output SOT-5 | 74AHCT1G125 | -NA- | 4.5-5.5V
U10 | Digi-Key | ADUM7441ARQZ-RL7TR-ND | Analog Devices | ADUM7441ARQZ-RL7 | ADUM7441ARQZ | 1.0 |  | ADUM7441 | QSOP16 | 4ch iCoupler | General Purpose Digital Isolator 1000Vrms 4 Channel 1Mbps 15kV/µs CMTI 16-SSOP (0.154", 3.90mm Width) | ADUM7441ARQZ | NA | 5V 1000Viso
U11 | Digikey | NCP160AMX330TBGOSTR-ND | On Semi | NCP160AMX330TBG | IC REG LINEAR 3.3V 250MA 4XDFN | 1.0 |  | LDO 3.3V 250mA | XDFN4 1X1 | IC REG LINEAR 3.3V 250MA 4XDFN | Linear Voltage Regulator IC Positive Fixed 1 Output 3.3V 250mA 4-XDFN (1x1) | LDO 3.3V 250mA | -NA- | 250mA
U12 | Digikey | 296-13961-2-ND | TI | SN74LVC125ARGYR | IC BUS BUFF TRI-ST QD 14VQFN | 1.0 |  | SN74LVC125A | PVQFN14_3.5X3.5 | IC BUS BUFF TRI-ST QD 14VQFN | Buffer, Non-Inverting 4 Element 1 Bit per Element Push-Pull Output 14-VQFN (3.5x3.5) | SN74LVC125A | -NA- | 1.65-3.6Vcc, 5V tolerant inputs
U13 | Digikey | W25X20CLUXIGTR-ND | Winbond | W25X20CLUXIG TR | IC FLASH 2MBIT 104MHZ 8USON | 1.0 |  | 2Mb | USON8 2X3 | IC FLASH 2MBIT 104MHZ 8USON | FLASH Memory IC 2Mb (256K x 8) SPI 104MHz 8-USON (2x3) | 2Mb | -NA- | 3.3V
X2 | Digi-Key | 609-1039-ND | FCI | 61729-0010BLF | USB-B | 1.0 |  | USB-B | PN61729 | USB connector B PTH | USB - B USB 2.0 Receptacle Connector 4 Position Through Hole, Right Angle | USB-B | NA | USB-B T-Hole R/A
X13 | Digi-Key | WM7837-ND | Molex | 0395311002 | 2POS | 1.0 |  | 0395311002 | MSTBV2 | Conn - 5.08mm Pitch Fixed | 2 Position Terminal Block Header, Male Pins, Shrouded (4 Side) 0.200" (5.08mm) Vertical Through Hole | 0395311002 | NA | 300V 15A 0.2"
X17 | Newark | 08N6789 | MultiComp | 2213S-06G | 6PIN | 1.0 |  | PINHD-2X3 | 2X03 | CONN HEADER VERT 6POS GOLD | 6 Positions Header Connector 0.100" (2.54mm) Through Hole Gold | 6PIN | NA | 10Pin 2Row 0.1" T-Hole
Y1, Y2 | Digi-Key | 887-1319-2-ND | TXC | 7M-16.000MEEQ-T | 16MHz | 2.0 |  | 7M-16.000MEEQ-T | CRYS320250 | Crystal 16mHz 10ppm 10pF | CRYSTAL 16.0000MHZ 10PF SMD | 16MHz | 10ppm | 10ppm 10pF 80R

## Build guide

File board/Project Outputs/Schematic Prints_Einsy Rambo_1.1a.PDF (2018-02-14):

D | D
C | C
B | B
A | A

Cannot open
file
C:\Users\Aaron\
Documents\Libs
\Sch Template
UMLogo\logo_
Project: Einsy Rambo | Ver: 1.1 a
Title: * | File: Title.SchDoc
Drawn by: UltiMachine | Sheet: 1 of 11

# Einsy Rambo 1.1a

9/18/2017

# UltiMachine

0.3a Revision Summary (for detailed infomation goto: https://github.com/ultimachine/Einsy-Rambo/tree/0.3a
- Added TVS and over-voltage protection to select nets
- Added and corrected testpoints
- Added "XTRA0" net between 32U2 and 2560
- Removed via tenting underneath QFNs and other flat solder lug/heatsink primitives
- Added teardrops to vias
- Standardized via sizes to 10/22 and 15/30 (mils)
- New footprint for 5V SMPS inductor (fits two inductors now)
- Added I2C pullup footprints (resistors are "DNI")
- Fan connectors now have a 3rd pin for reading the TACH signal

Notes:
DNI Do Not Include
- Added 100R to the gate of each FET
- Adjusted the stackup to better reflect a standard 4-layer stack
= | = No Populate
- Updated paste mask apertures on QFNs
- Increased copper pour coverage
- Increased GND stitching
- Moved thermistor TPs to connector pin
- New footprint for P3
- Touchup diode polarity markings in silkscreen
- Removed RN4
- Added R73
- Added nAC_FAULT to pin_6 of Atmega2560
- Combined 2560 ICSP (X18) with pins_9-14 of J19
- Stole RX1 and TX1 from P1, moved to J19
- Added J7, power failure relay input.
- Removed J16-J18, X_MAX, Y_MAX, Z_MAX

0.4a Revision Summary

- Changed X_MIN and Y_MIN endstops to 2-pin headers
- Changed Z_MIN endstop to Z_PROBE, 4-pin header
- Combined DIAG_0 and DIAG_1 on TMC2130 drivers
- TP40 moved 0.1" to the left
- TP32 moved 0.1" to the left

0.5a Revision Summary
- Added ferrites to motor controller outputs.
- Removed fuse and input filter for VMOT
- Move MOSFET pulldown resistors to input side of AND gates
- Added ferrites to all P1 and P2 signals.
- Changed RN1 and RN2 from 10k to 5.6k (increases voltage on motor controller Vref pins)
- Changed motor controller low-side I-sense resistors from 0.1 to 0.22Ohm
- Voltage regulator U3 is now sourced from VMOT (was +12V2)
- Added power bypass capacitors to J7 and J15
- +12V2(Logic) and +12V3(Bed) now have micro-controller ADC based voltage monitoring.
- Added filtered internal island for micro-controller Vcc
- Added 2 internal layers (now 6 layers total)
- Most bottom layer routing (Layer 6) was moved to the new adjacent internal layer (Layer 5)
- Moved MOSFET pulldowns R43 and R57 upstream from FETs and placed at input of AND gate.
- New pinout for J19 header.
- Motor connectors are now flush with the bottom edge of the board.

1.0a Revision Summary
- Populate FGND to GND resistor ties

1.1a Revision Summary
- Added 2Mb serial flash
- Added voltage translators for serial flash
- Added tri-state buffer to block 3.3V MISO on the SD Card from the 5V MISO bus
- Added barrel-relief to bottom side of thermal vias for TMC2130, FETs and SMPS
- Added 3.3V LDO for serial flash

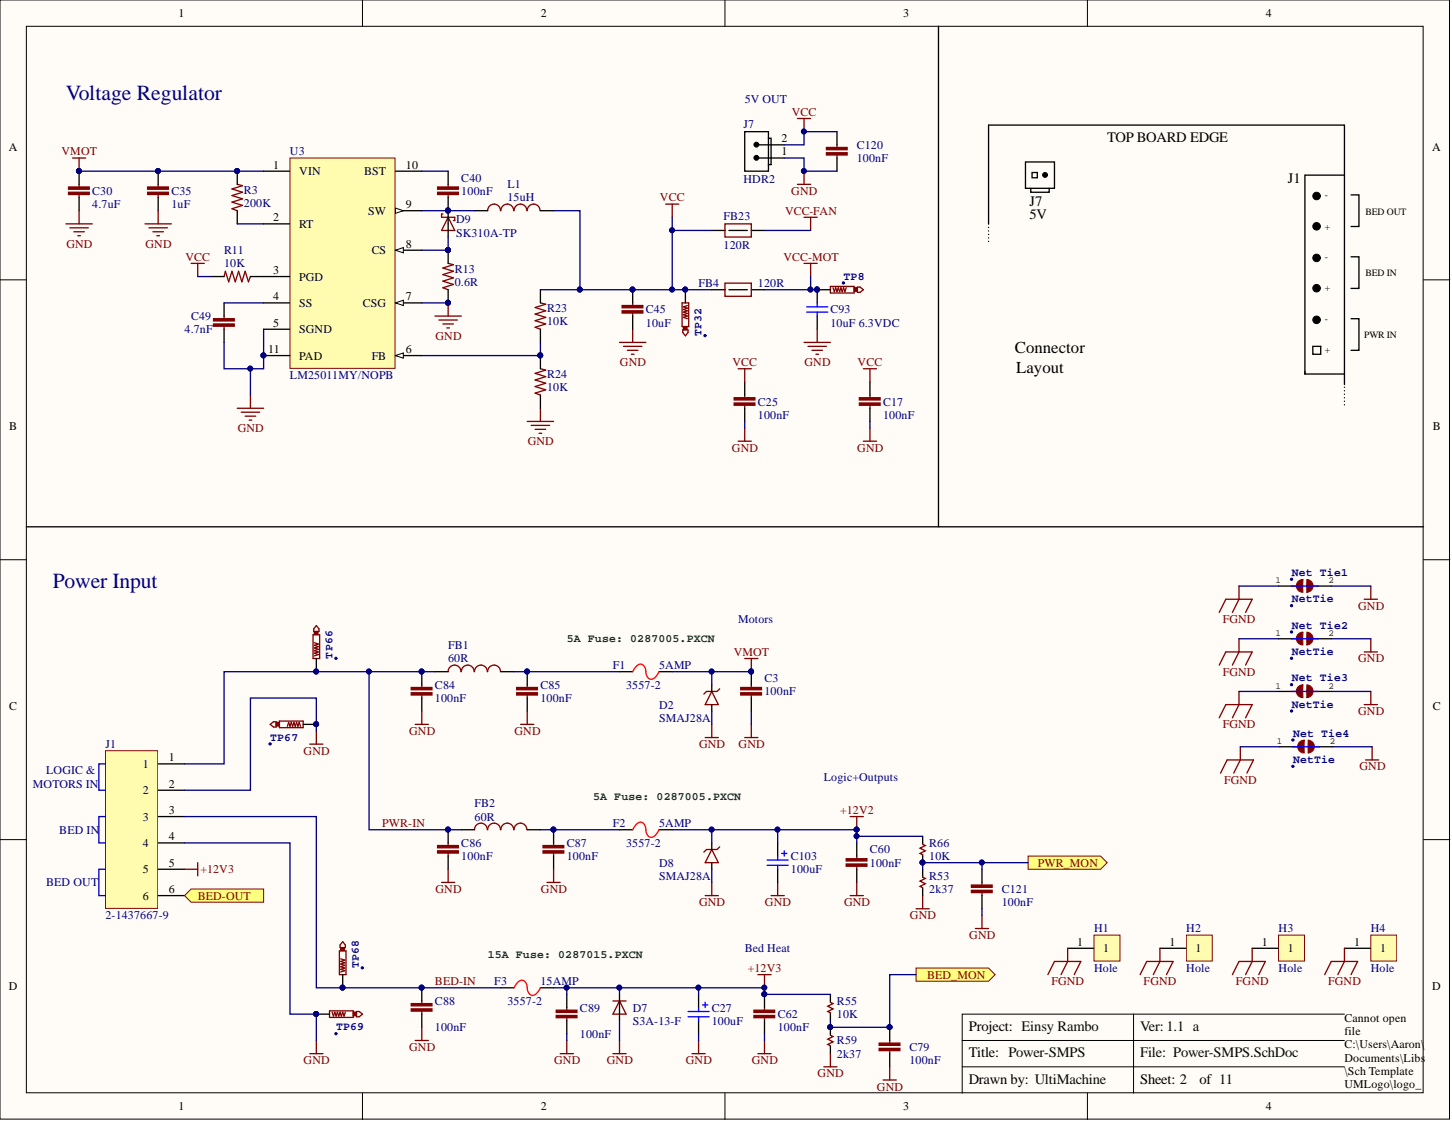
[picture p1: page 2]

Project: Einsy Rambo | Ver: 1.1 a

Power-SMPS | Power-SMPS.SchDoc

UltiMachine | 2 11

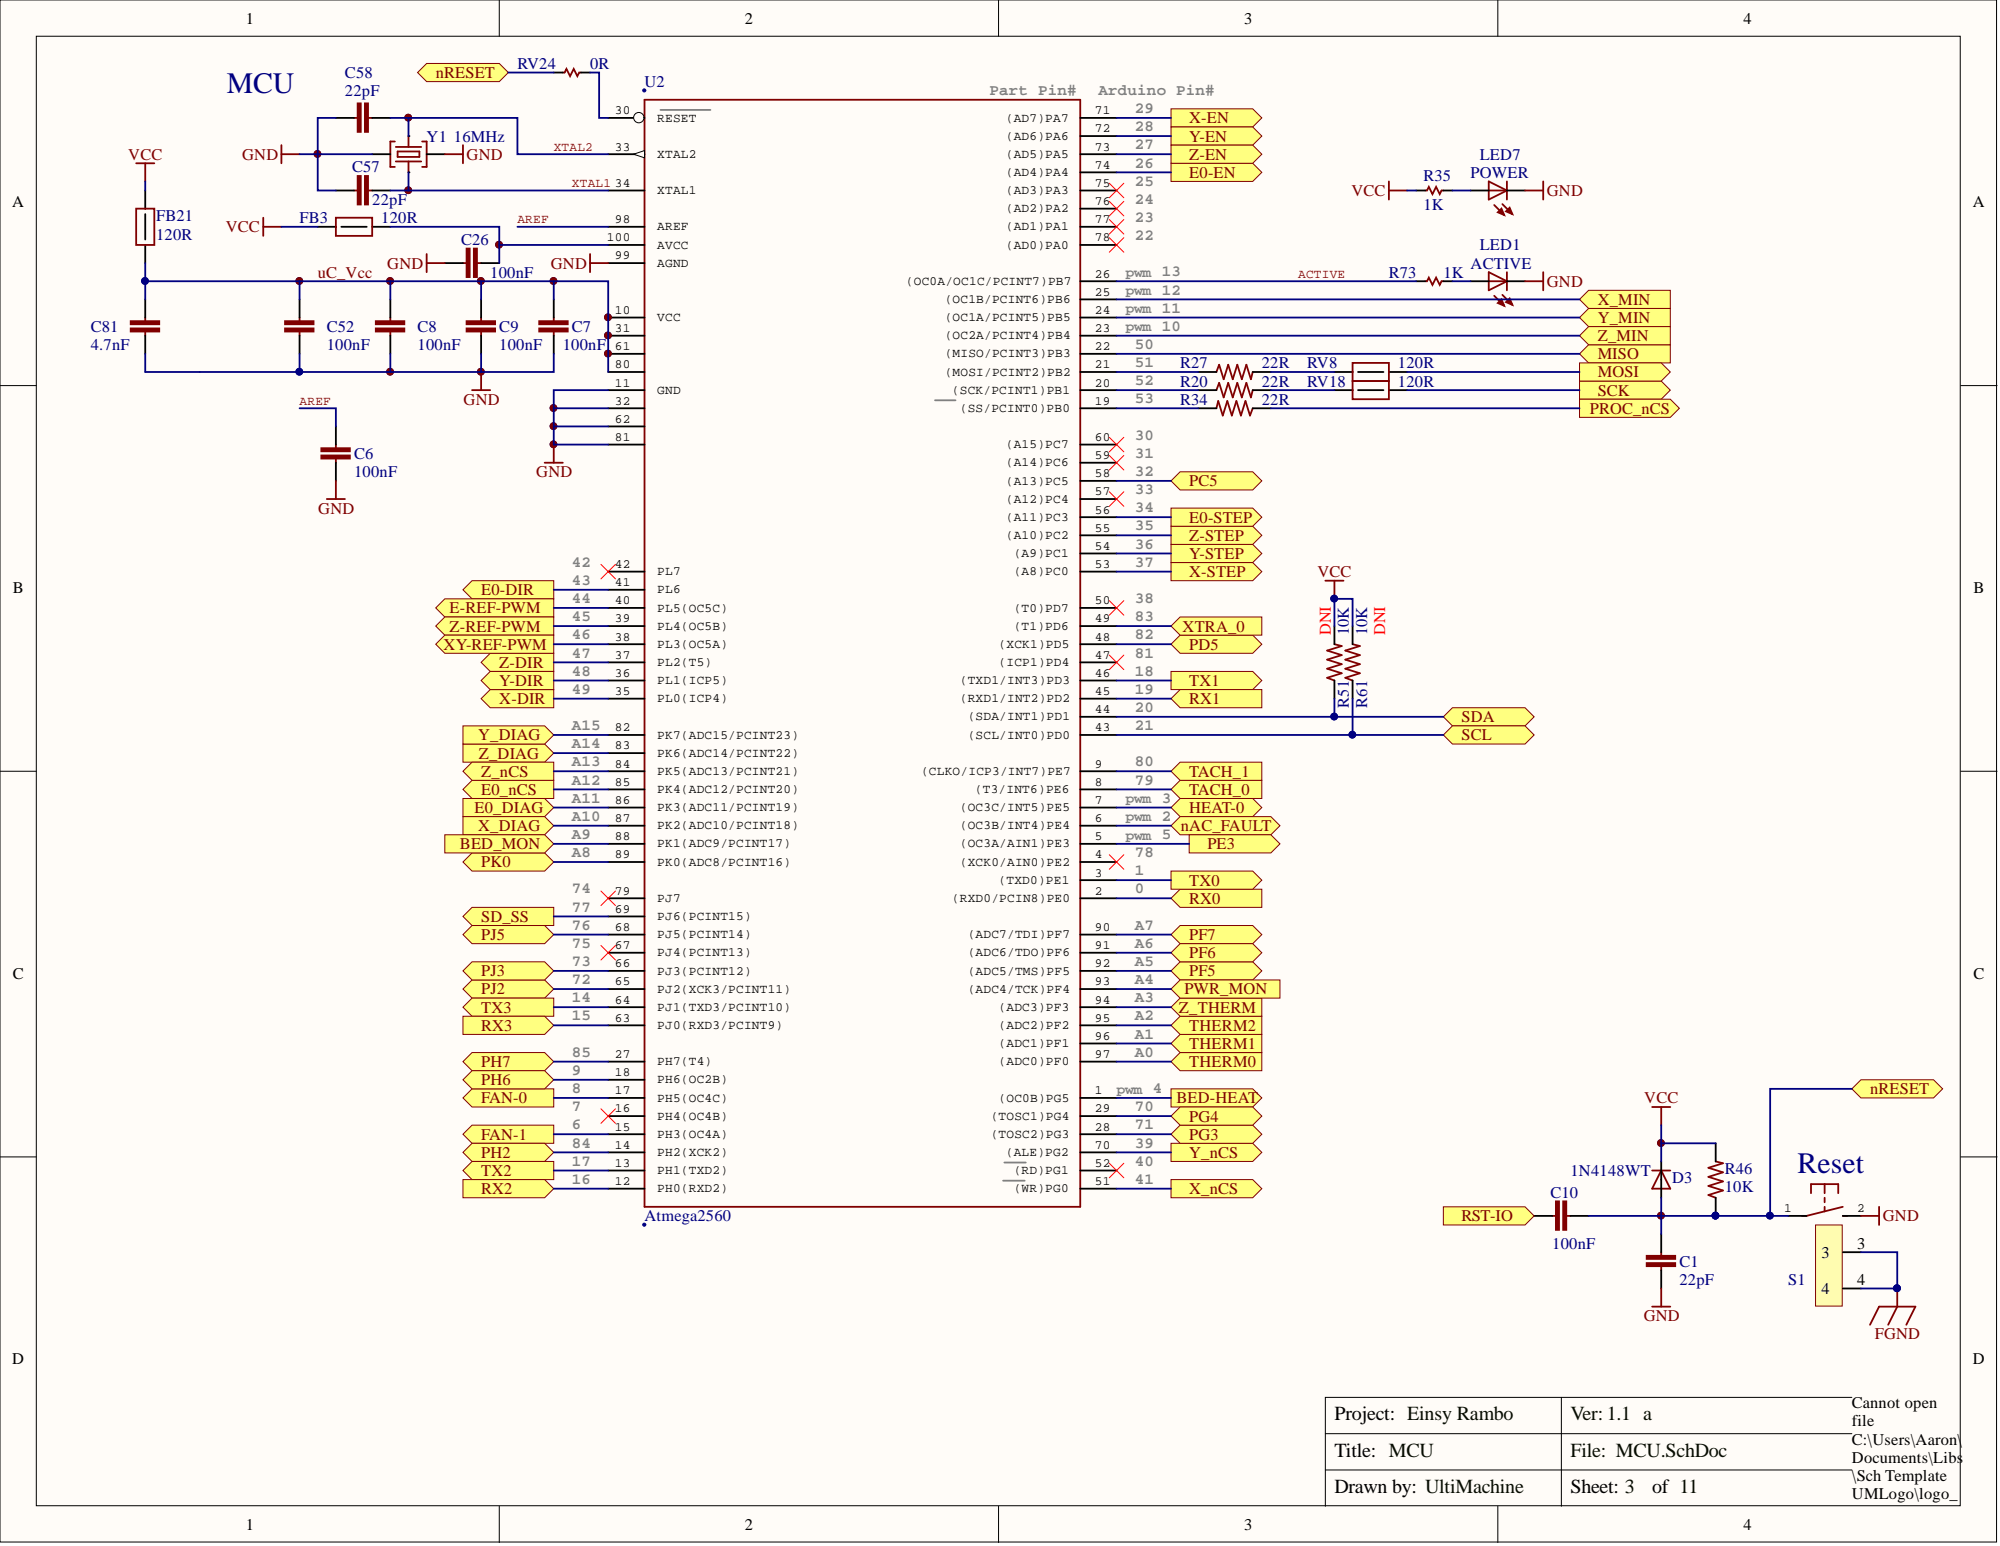
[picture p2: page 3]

32
62
81

Project: Einsy Rambo | Ver: 1.1 a

MCU | MCU.SchDoc

UltiMachine | 3 11

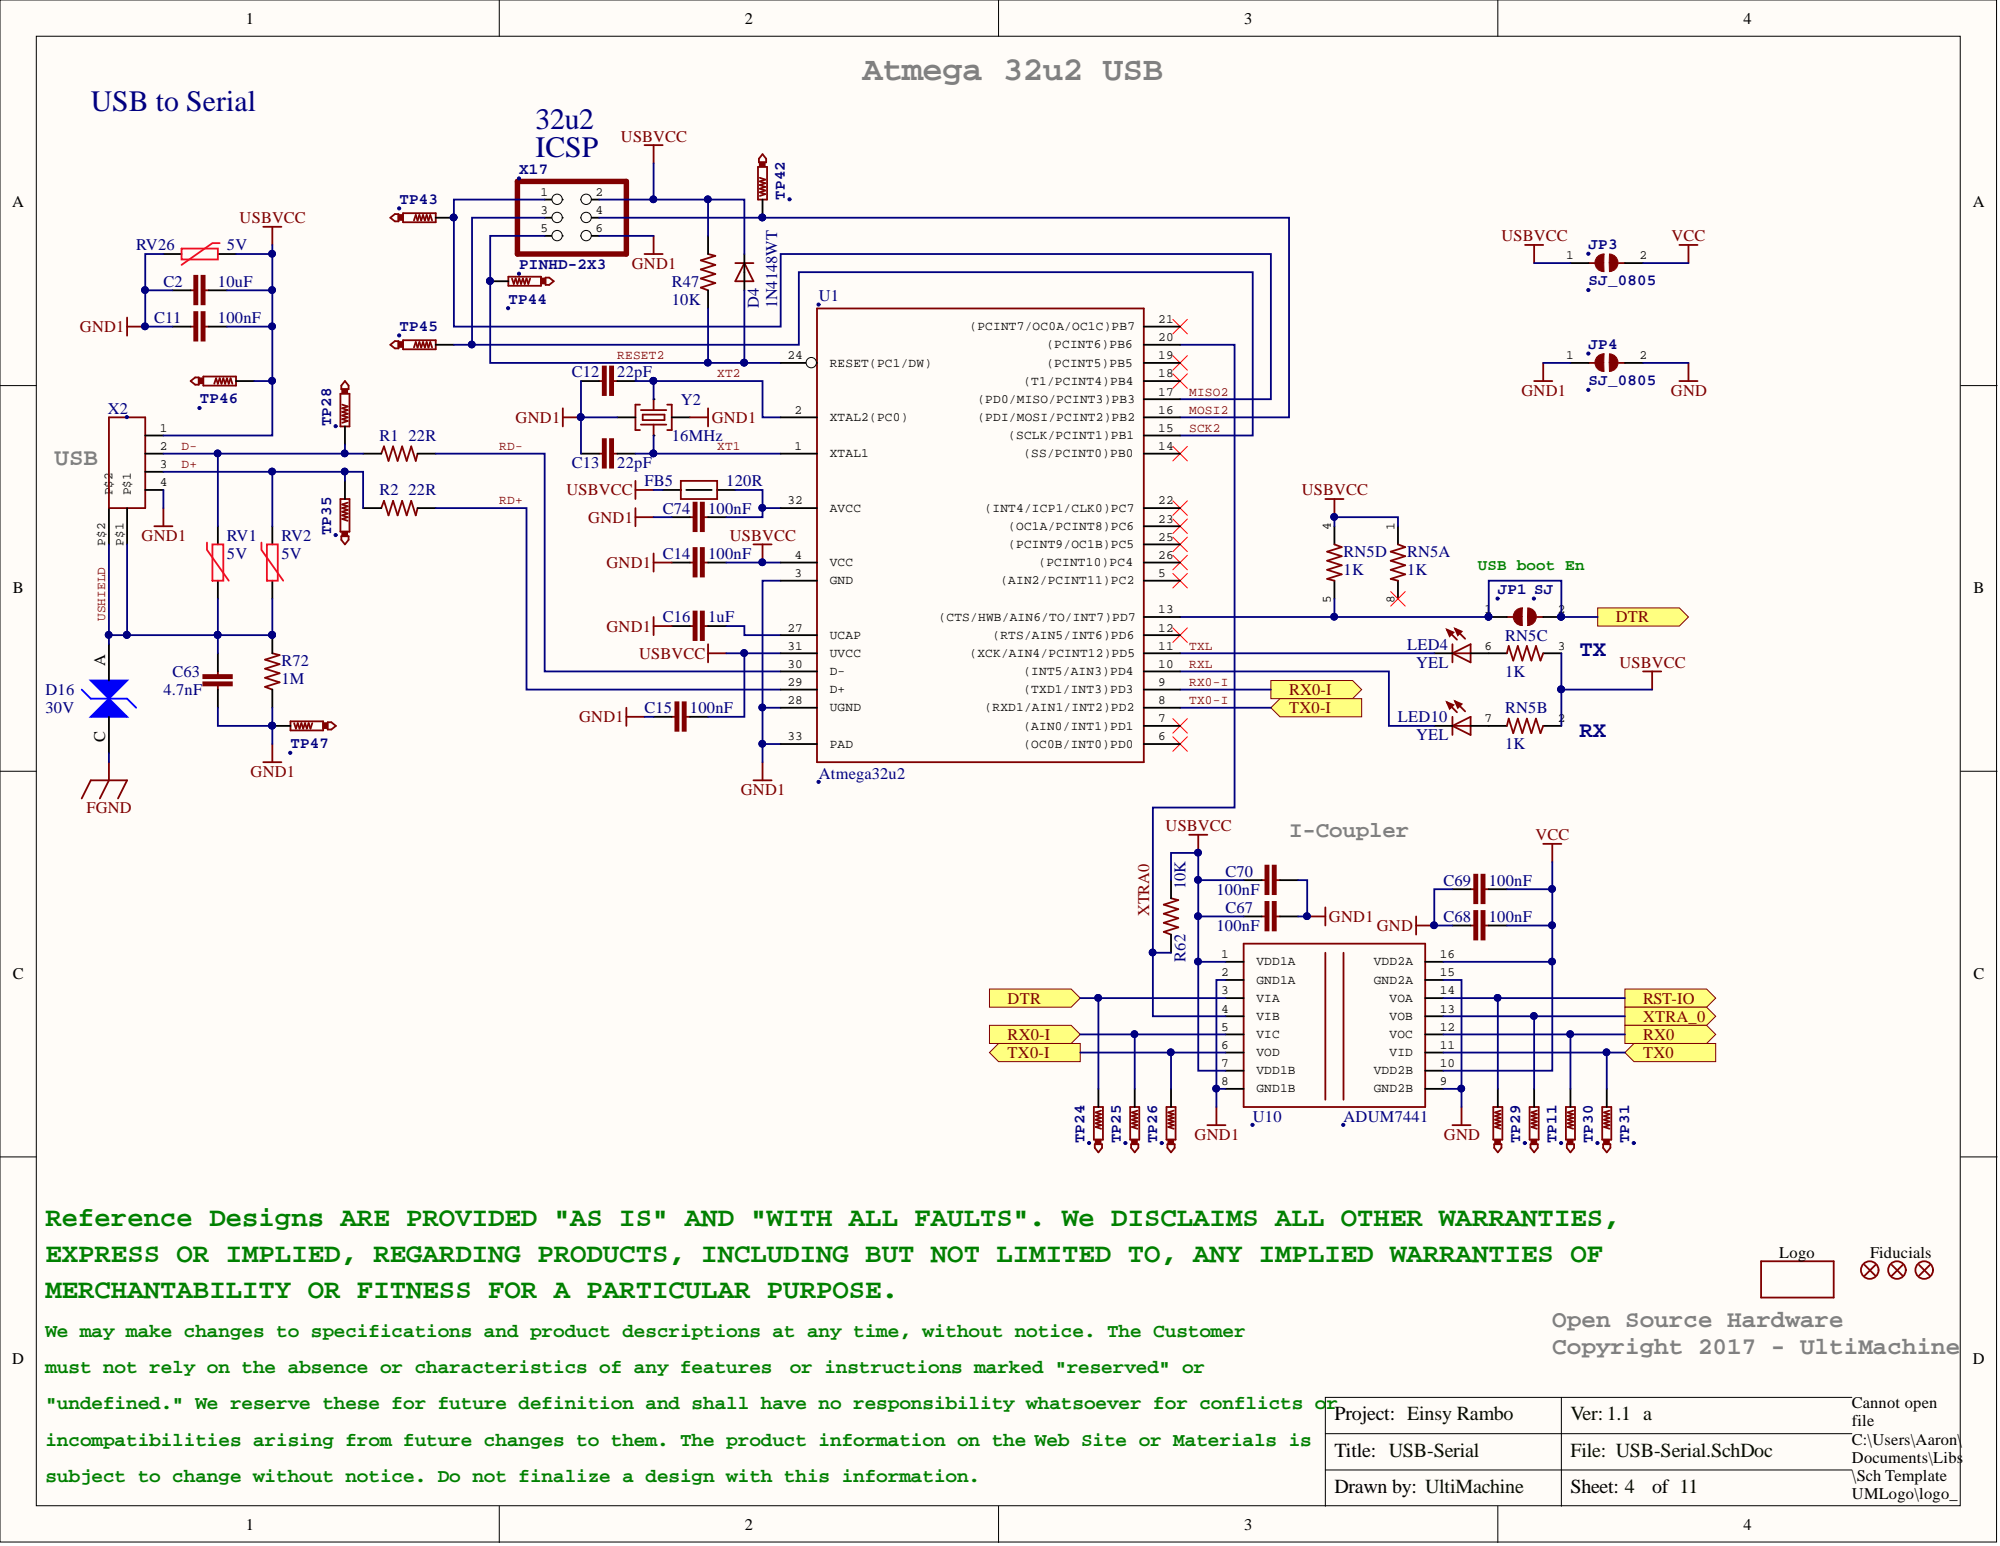
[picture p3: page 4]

3 4
5 | 6 | R47

VDD1A 1
GND1A 2

Reference Designs ARE PROVIDED "AS IS" AND "WITH ALL FAULTS". We DISCLAIMS ALL OTHER WARRANTIES,
EXPRESS OR IMPLIED, REGARDING PRODUCTS, INCLUDING BUT NOT LIMITED TO, ANY IMPLIED WARRANTIES OF
MERCHANTABILITY OR FITNESS FOR A PARTICULAR PURPOSE.

We may make changes to specifications and product descriptions at any time, without notice. The Customer
must not rely on the absence or characteristics of any features

or instructions marked "reserved" or

"undefined." We reserve these for future definition and shall have no responsibility whatsoever for conflicts or

Project: Einsy Rambo | Ver: 1.1 a

incompatibilities arising from future changes to them. The product information on the

Web Site or Materials is

USB-Serial | USB-Serial.SchDoc

subject to change without notice. Do not finalize a design with this information.

UltiMachine | 4 11

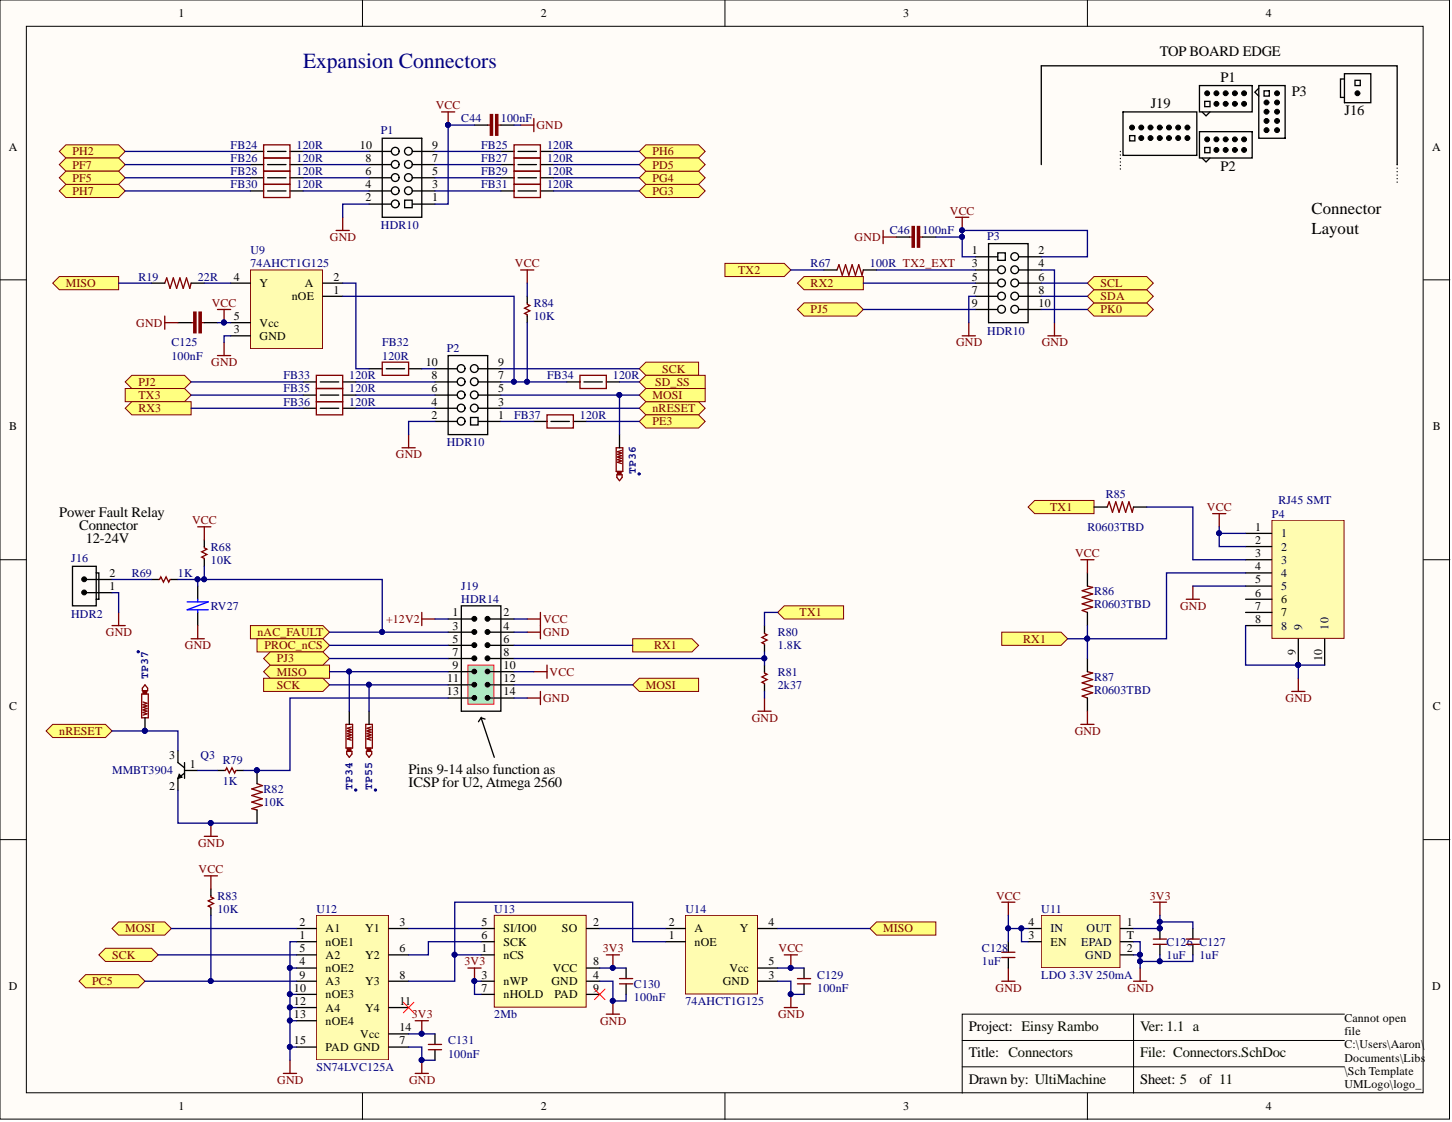
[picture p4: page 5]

Pins 9-14 also function as
ICSP for U2, Atmega 2560

nCS 1

nOE3 10 nOE4 13 PAD 15 | | nHOLD 7

Project: Einsy Rambo | Ver: 1.1 a

Connectors | Connectors.SchDoc

UltiMachine | 5 11

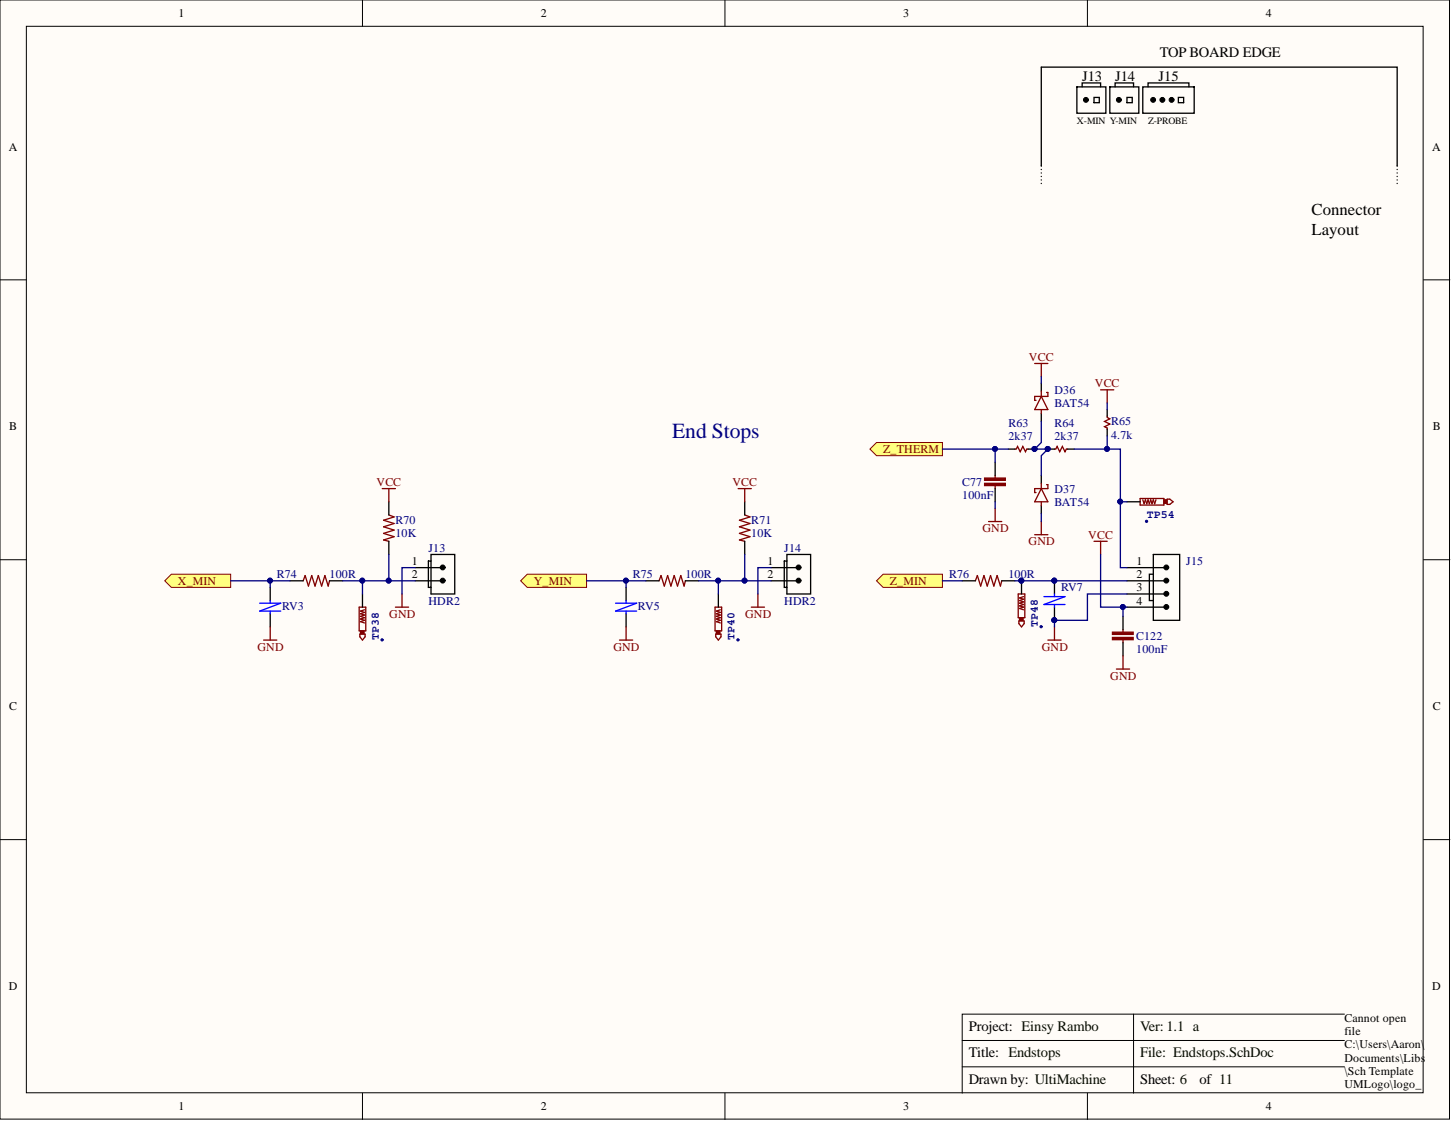
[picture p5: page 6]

Project: Einsy Rambo | Ver: 1.1 a

Endstops | Endstops.SchDoc

UltiMachine | 6 11

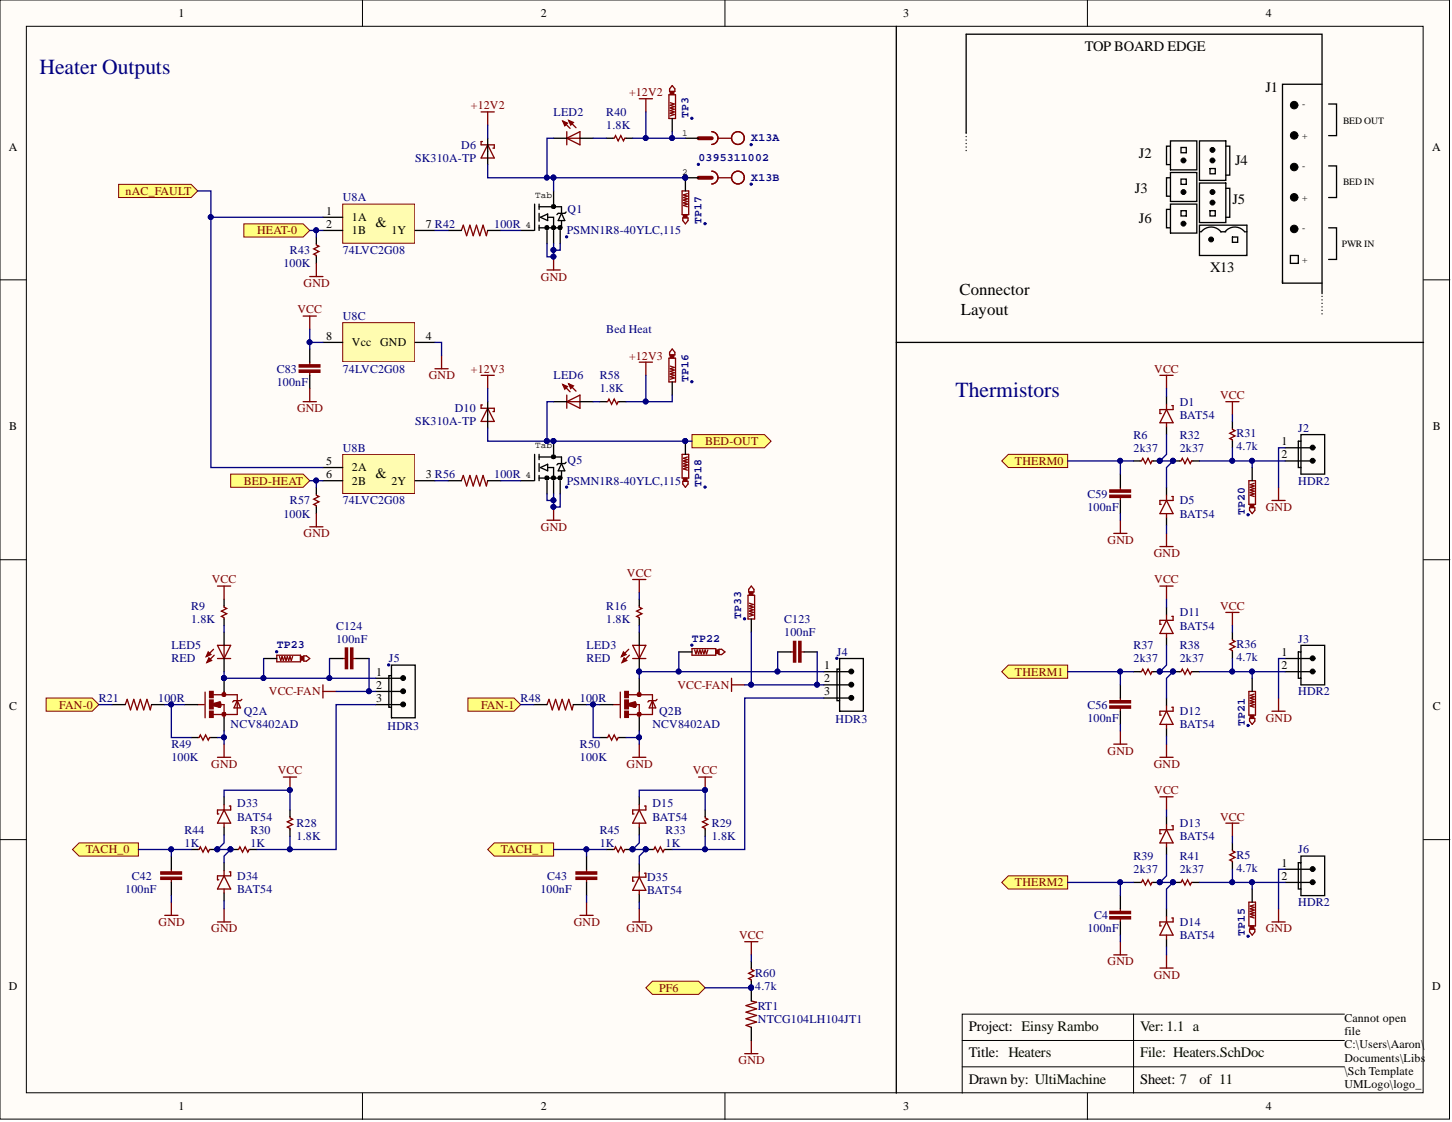
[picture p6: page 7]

Project: Einsy Rambo | Ver: 1.1 a

Heaters | Heaters.SchDoc

UltiMachine | 7 11

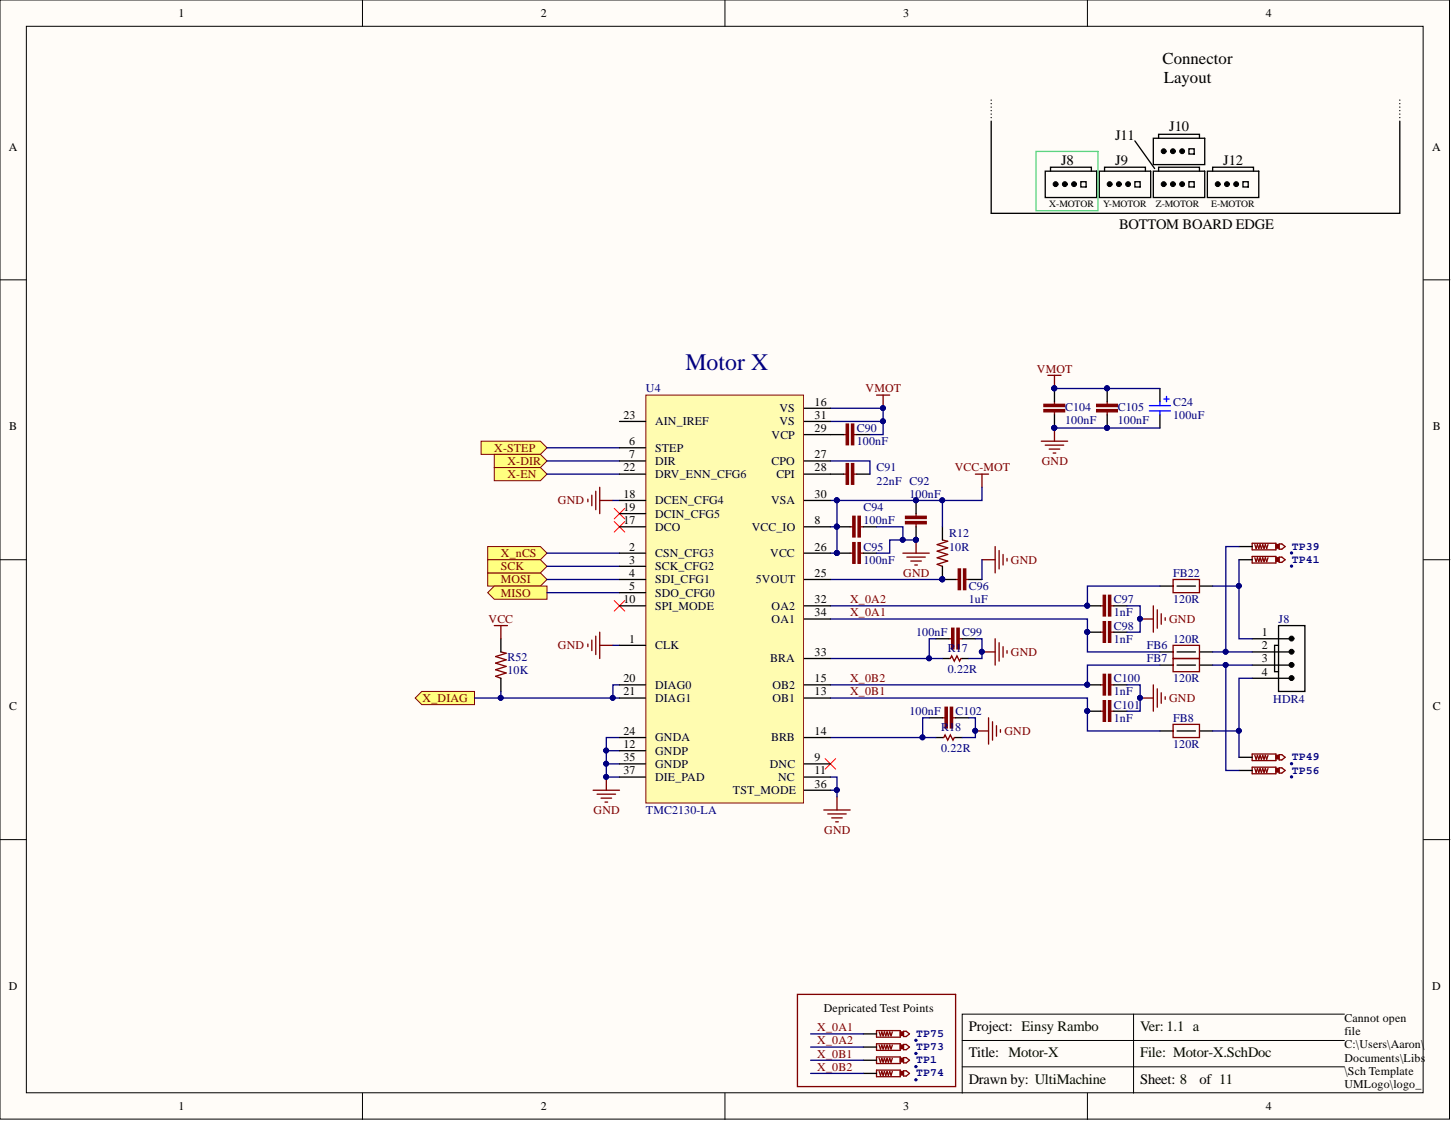
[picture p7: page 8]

CLK 1 | X_0A1

DIAG1 21 GNDA 24 | X_0B1

Project: Einsy Rambo | Ver: 1.1 a

Motor-X | Motor-X.SchDoc

UltiMachine | 8 11

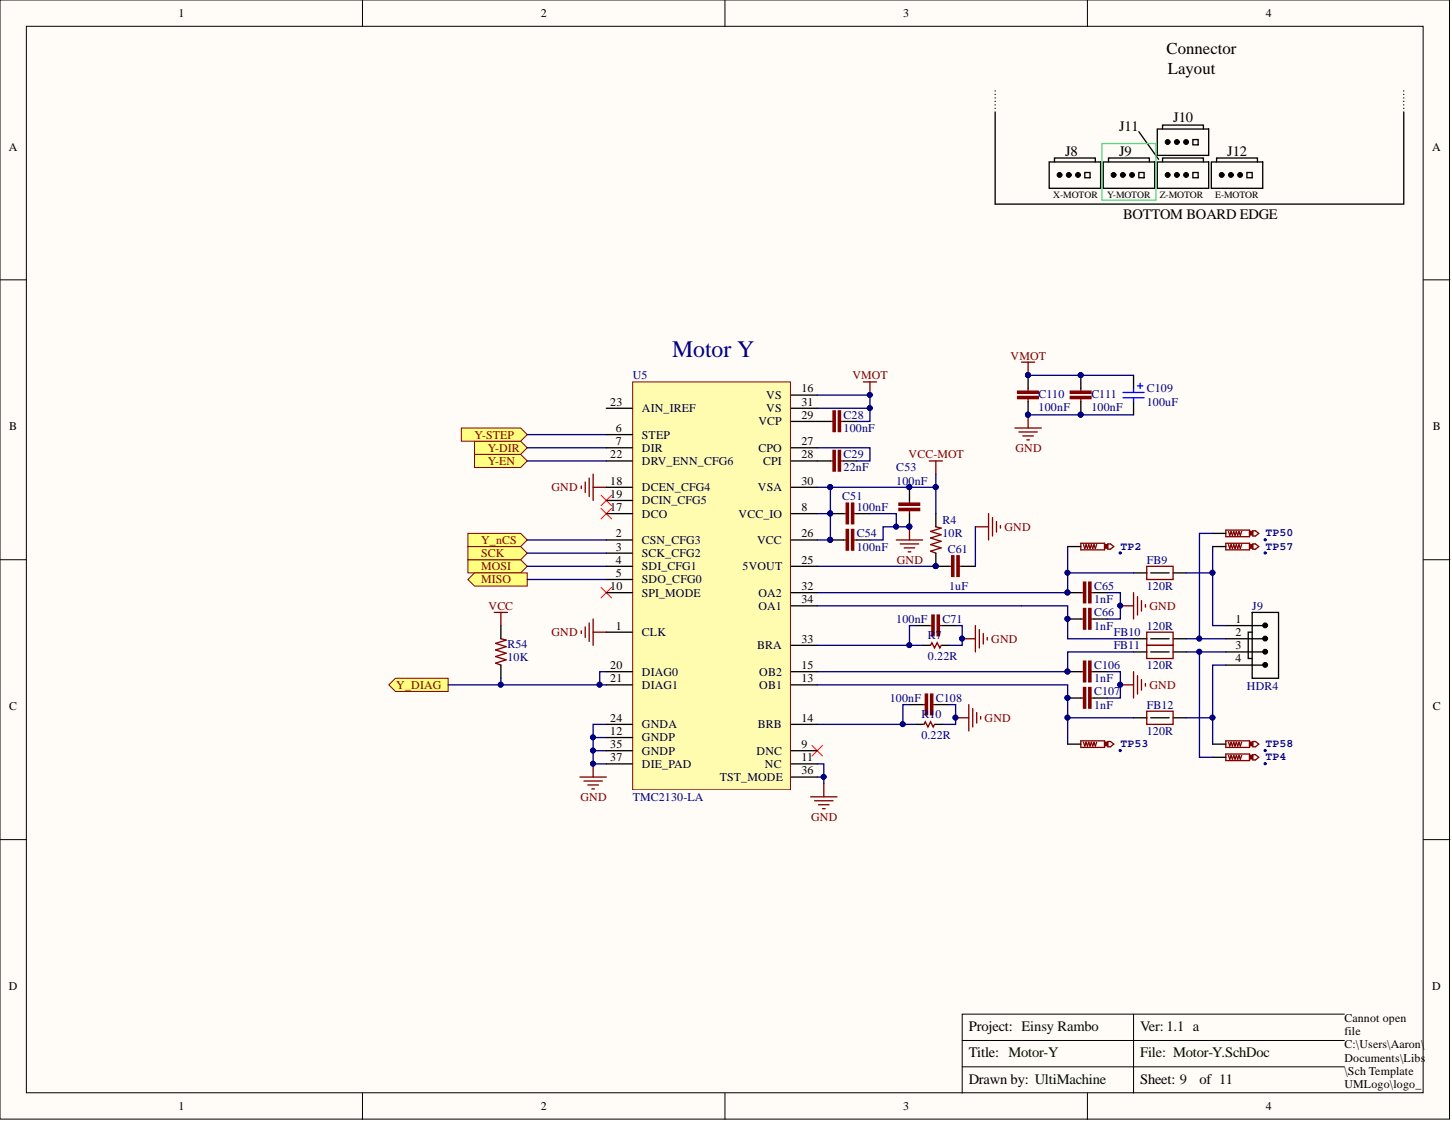
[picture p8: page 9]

Project: Einsy Rambo | Ver: 1.1 a

Motor-Y | Motor-Y.SchDoc

UltiMachine | 9 11

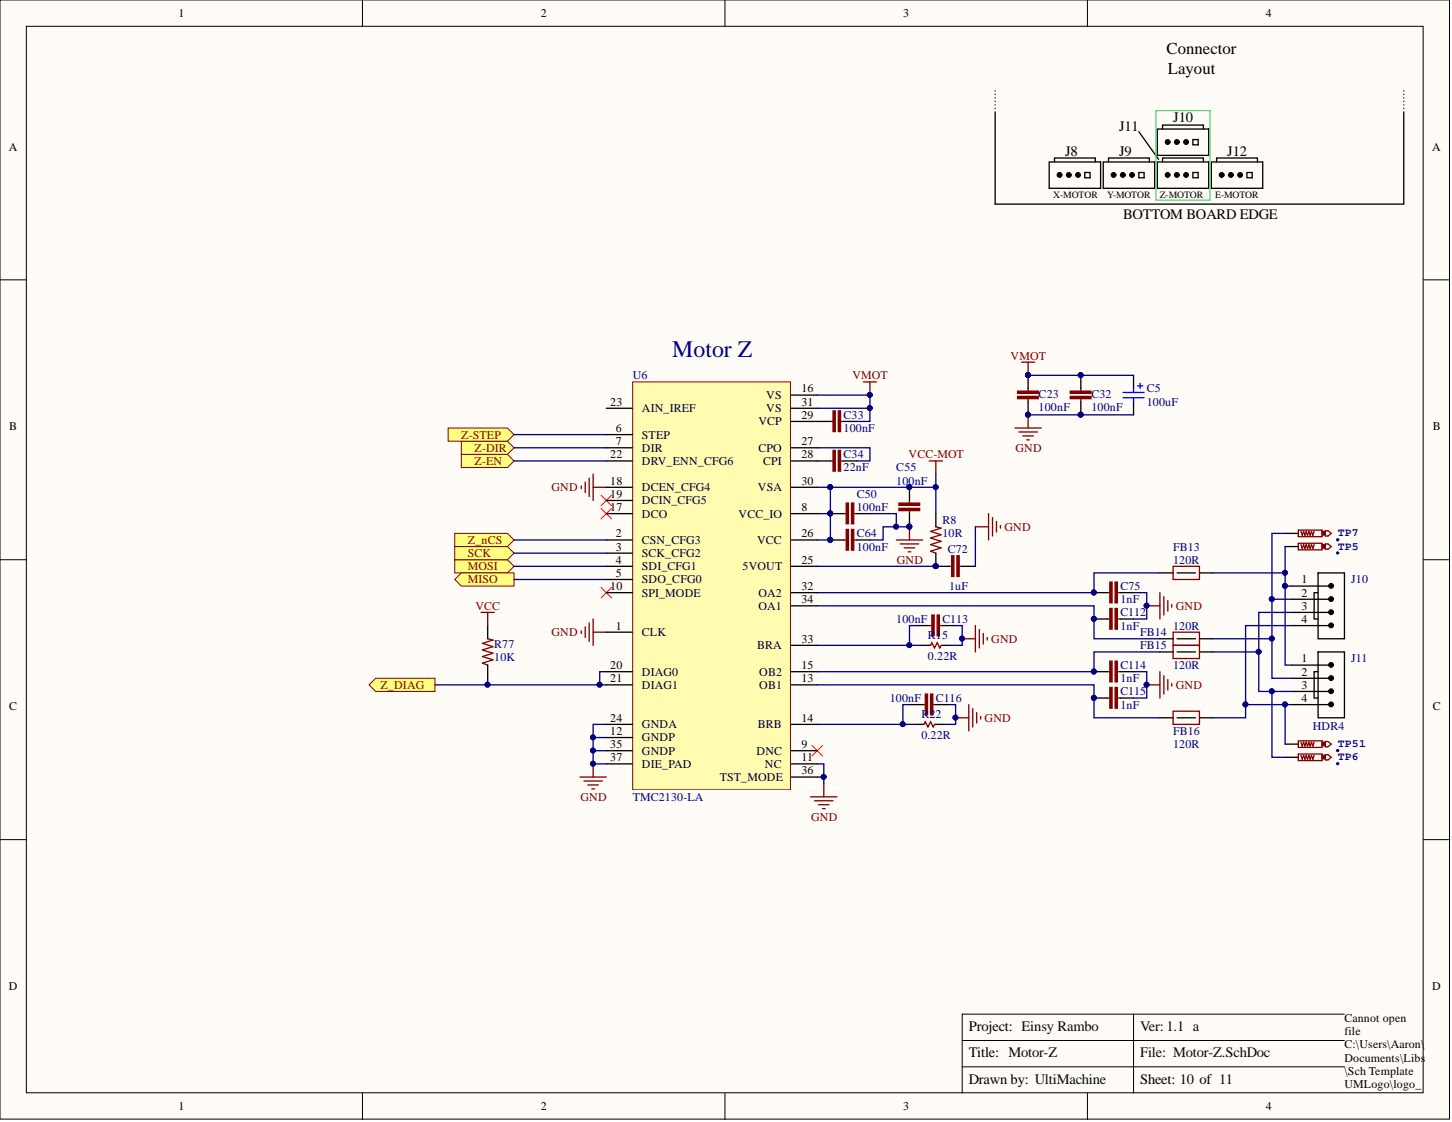
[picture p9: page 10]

Project: Einsy Rambo | Ver: 1.1 a

Motor-Z | Motor-Z.SchDoc

UltiMachine | 10 11

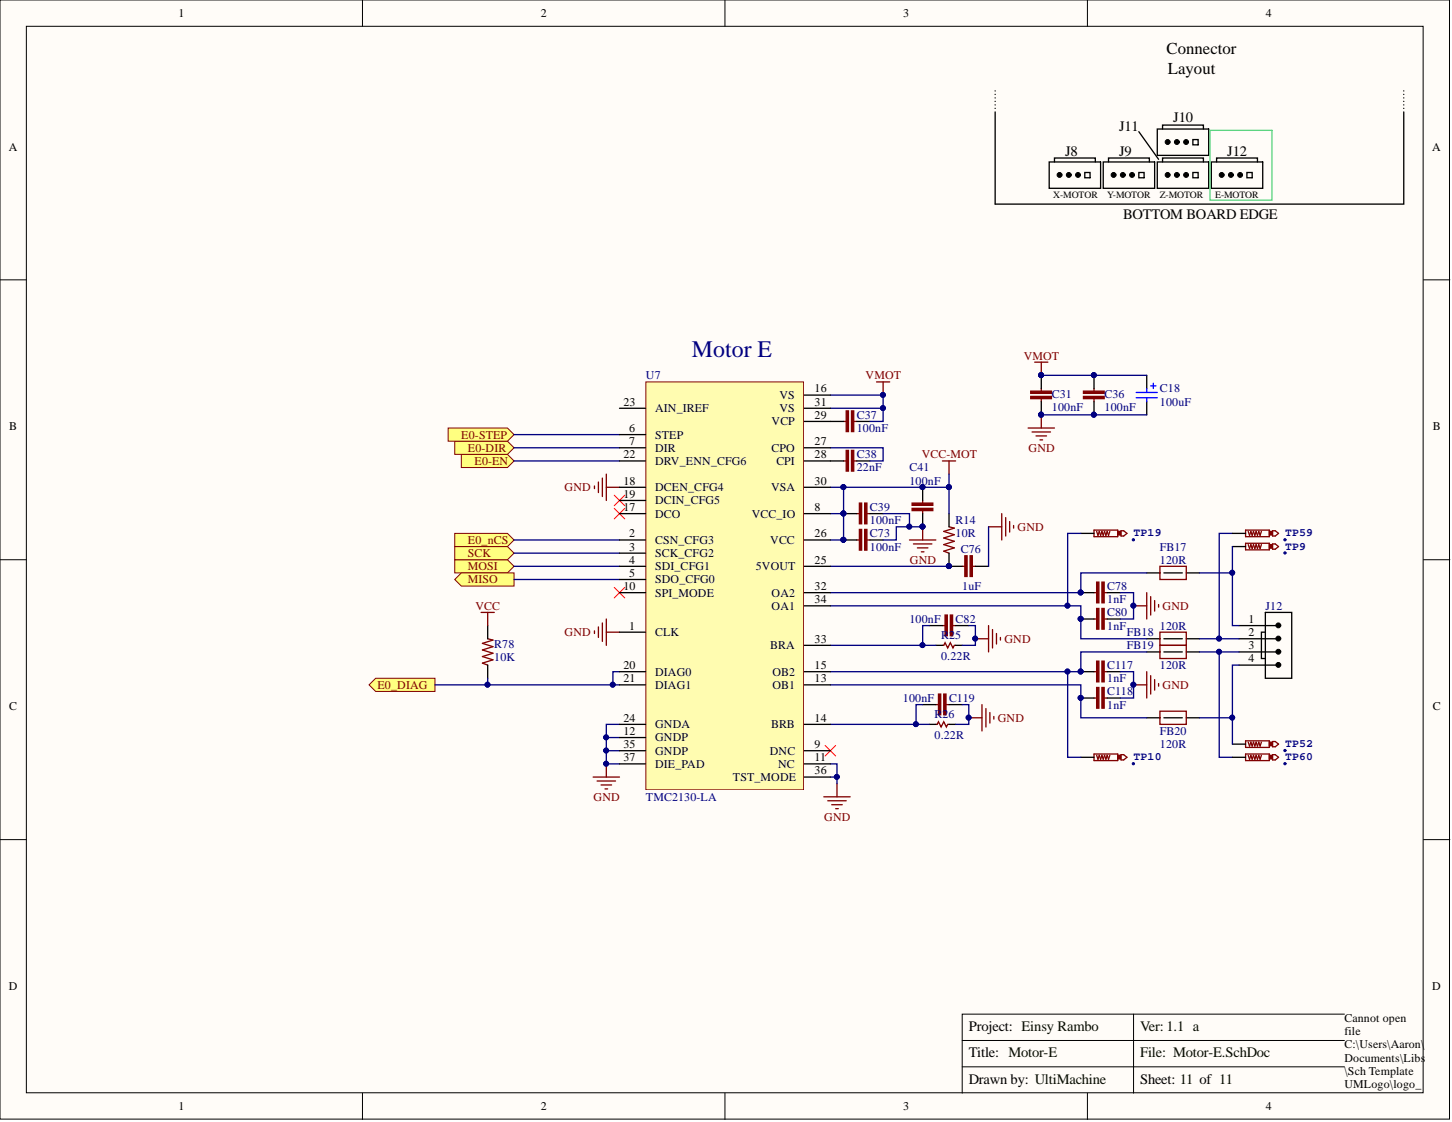
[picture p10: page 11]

Project: Einsy Rambo | Ver: 1.1 a

Motor-E | Motor-E.SchDoc

UltiMachine | 11 11

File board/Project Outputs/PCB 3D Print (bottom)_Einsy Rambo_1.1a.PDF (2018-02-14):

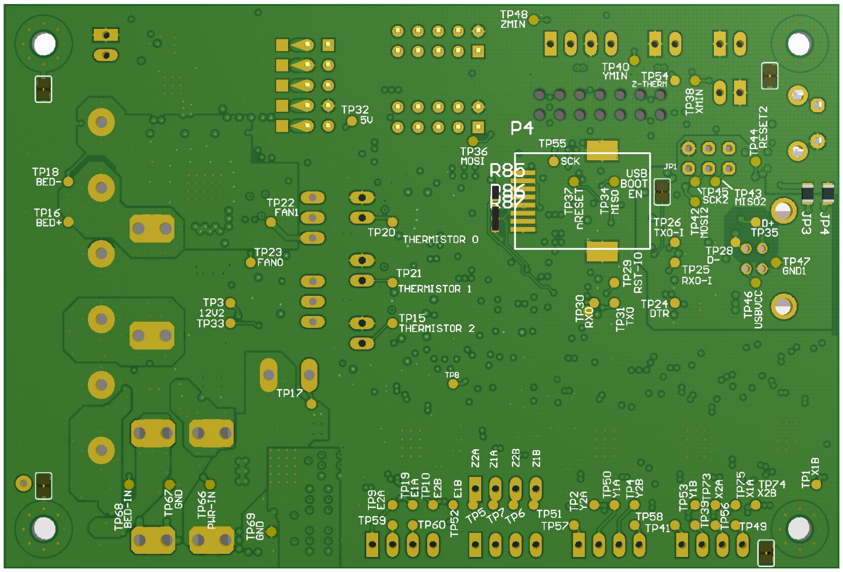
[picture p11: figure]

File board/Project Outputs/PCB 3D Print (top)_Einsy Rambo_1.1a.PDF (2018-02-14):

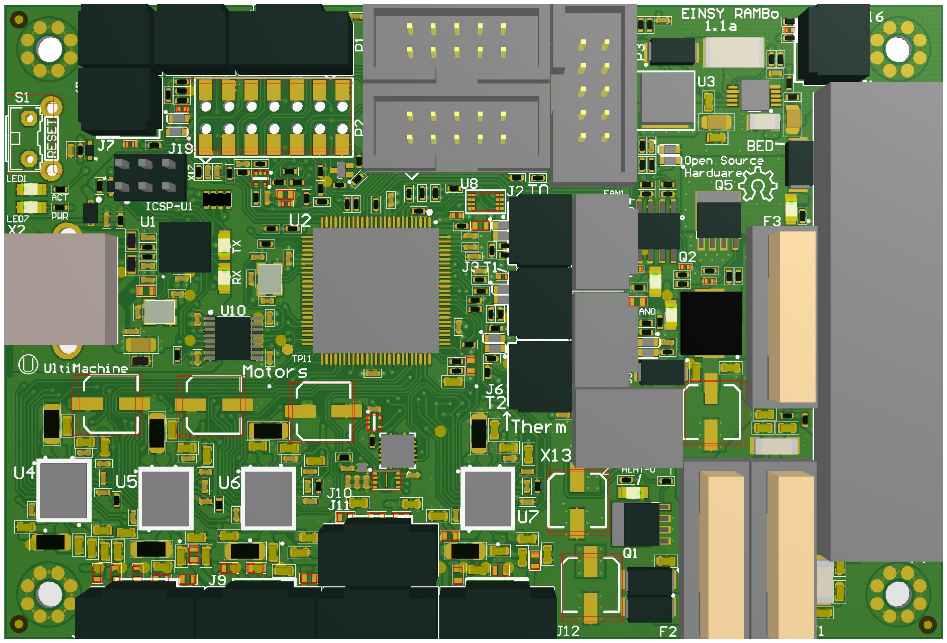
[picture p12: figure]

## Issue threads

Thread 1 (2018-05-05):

Z-AXIS MOTOR CURRENT

danman454, 2018-05-05:
Hey All. I'm trying to upgrade my printer with the Einsy Rambo 1.1 and it's been quite the challenge for me. I'm fairly new with this stuff and still learning. The issue i'm having right now is my z axis. The motors seem to be under powered. Both motors spin together but barely holding the shaft stops them (motors pulled from printer). The board i had before was the Mks base 1.5 which gave the motors a ton of torque. It was easier to adjust on the mks board because the drivers had trimpots. The Einsy does not. Any help would be appreciated. i've added my confg.h and confg.adv.h Thanks!
[Marlin.zip](https://github.com/ultimachine/Einsy-Rambo/files/1976425/Marlin.zip)

Elocai, 2018-05-11:
it´s even easier on the einsy because it does not (use any trimpots).

just go check your configuration advanced file, look for the tmc2130 setting, there is a value for current which you just have to type in, and a factor for holding current, and a mode select for spreadcycle for more reliability and...and....and.... : )

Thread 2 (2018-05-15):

Flashing via ISP

dounix, 2018-05-15:
I bought a einsy-rambo directly from ultimachine to use while prusa took their time sending me a replacement board.   It worked fine with prusa 3.1.3, but 3.2.0 doesn't seem to fit, so I was trying to put the prusa bootloader on it via ISP.

I can't seem read/write the flash(for changing bootloader) on my einsy-rambo 1.1a via ISP.

The schematics show the bottom half of J19 used for ISP, verified gnd/vcc pins before attempting.
Sheet 5 of https://github.com/ultimachine/Einsy-Rambo/blob/1.1a/board/Project%20Outputs/Schematic%20Prints_Einsy%20Rambo_1.1a.PDF

Using avrdude  and a USBASP programmer(double checked the programmer on a few of AVR dev boards I have around)

Tried using power from the programmer, and externally powed(with power disabled on the programmer of course)

avrdude fails to get a device signature all 0's whenpowered by the programmer, all f when externally powered.

All connectors are unplugged, only the ISP plugged in.

Wanted to ask is there Is there a trick to getting it to program?
Jumpers or pullups/downs on miso/mosi?

darkdelphi, 2018-05-19:
I have the same exact issue. I was able to get a previous RC1 build to work at one point but accidentally deleted it.  I went back to 3.13 for some reason I can't remember but now I can't get any of the 3.2 versions to work constantly getting mismatch errors

tonokip, 2018-05-21:
@dounix
The reset signal on J19 is inverted. If you use the one on the P2 header it should work.

@darkdelphi
Regarding mismatch errors, I believe this could be due to a changes in the prusa-stk500v2 bootloader versus the Arduino Mega version. The mismatch seems to happen when trying to use close to ~96%+ of the flash space.

patelmontu, 2019-02-12:
I bought a einsy-rambo 1.1b directly from ultimachine to use in my custom made printer.
As per ultimachine website A preconfigured Marlin Firmware is preloaded onto the board But when I connect the board with RepRapDiscount Full Graphic Smart Controller its just blank no light  nothing and I check the power led is on.
And I just swep the EXP1 and EXP2 cable then LCD light is on but blank.

So how to find which firmware is preloaded and which configuration.

I just try to upload new firmware from Ultimachine Github (https://github.com/ultimachine/Marlin/tree/Einy-Rambo/Marlin) using Aurduino 1.8.7 I got the error massage (Arduino: 1.8.7 (Windows 10), Board: "RAMBo"

Sketch uses 94090 bytes (36%) of program storage space. Maximum is 258048 bytes.
Global variables use 4595 bytes of dynamic memory.
Error opening serial port 'COM15'. (Port busy)
avrdude: stk500v2_ReceiveMessage(): timeout
avrdude: stk500v2_ReceiveMessage(): timeout
avrdude: stk500v2_ReceiveMessage(): timeout
avrdude: stk500v2_ReceiveMessage(): timeout
avrdude: stk500v2_ReceiveMessage(): timeout
avrdude: stk500v2_ReceiveMessage(): timeout
avrdude: stk500v2_getsync(): timeout communicating with programmer
An error occurred while uploading the sketch

This report would have more information with
"Show verbose output during compilation"
option enabled in File -> Preferences.)

I need Help.

Regards,
Mayank .

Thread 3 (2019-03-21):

info bltouch end stop

shiryu55, 2019-03-21:
You could indicate to me awkward a couple of doubts.

My doubts, to configure marlin 2.0, configure it with bltouch, since I will not put the magnetic bed.

looking on the internet I found how the bltouch would connect.

Configuration.h settings:

DEFINE Z_MIN_PROBE_USES_Z_MIN_ENDSTOP_PIN
DEFINE Z_ENDSTOP_SERVO_NR 0 // DEFAULTS TO SERVO 0 CONNECTOR.
DEFINE Z_SERVO_ANGLES {10.90} // Z SERVO DEPLOY AND STOW ANGLES
DEFINE NUM_SERVOS 1
Remap pins_EINSYRAMBO.h

DEFINE SERVO0_PIN 10
DEFINE Z_MIN_PIN 11 // Y-MIN ON BOARD.

but I would lose the connection pin for y axis.

finally, how the power of the 2130 and the virtual limit switches are configured.

If it is not too much work , you could send me a marlin 2.0, preconfigured  for this board ,to start from this. in marlin 2.0 examples not included rambo 1.1 board.

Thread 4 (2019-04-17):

Reprap Wiki Doku error

Detzi88, 2019-04-17:
Hi,
i noticed that in the pinout drawing "EinsyRambo1.1a-connections.jpg" [(here)](https://reprap.org/wiki/EinsyRambo) has misleadingly labeld fan and "Bed Output" (i did not check further) connectors.
These are labeled "S", "5V" and "-" and "+" and "-". The common ground on the power input is also labeled "-" this indicates the same net on all those "-" labeled Connectors. I suggest renaming them in something like "o" + the number of the connector like "o1" for example.

I hope this is the right place to raise the issue i didn't find a better one so far.

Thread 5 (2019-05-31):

Power loss recovery configuration in marlin 1.1.9

patelmontu, 2019-05-31:
hello,

I Have a problem in Einsy board i build my own 3d printer using Einsy board, And I use Marlin-i3-MK3 firmware (https://github.com/prusa3d/Prusa-Firmware)
When I enable power loss recovery the print was start and just within one second it detect power loss and i click on resume print again print start and  go to the power loss recovery mode.

Closed 2020-06-10.

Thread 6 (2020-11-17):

Where is the branch 1.2b?

miracuruzrh, 2020-11-17:
Hi

I need your help. I have a Prusa i3 MK3/s with the Einsy Rambo 1.2b mainboard. But I am confused.
On the master branch I have found this information:

> "johnnyr generate assembly docs for 1.2b
> 5c79206"

 but when I download this branch I find only 1.2a mainboard schematics. Therefore can anyone help me out with the correct link ord schematics? Many thanks in advance

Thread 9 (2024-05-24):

Trying to send text out through serial port

RogerInHawaii, 2024-05-24:
I'm made modifications to the Marlin firmware for my Prusa i3 MK3. I added some new GCodes that are processed within the Marlin firmware at the process_commands() method. I know that it's getting to my new code. But when it's there I want it to send some text out through the TX pin on the J19 socket of the Einsy Rambo board. I THINK that I'm calling the correct MarlinSerial methods, like:

In setup():

    MarlinSerial::begin(115200);

In process_commands()

     where I'm processing my new GCode:

           MarlinSerial::println("Let us test a whole bunch of text going out through the serial port");
           MarlinSerial::flush(); // Ensure all outgoing data is sent

But nothing is happening at the TX pin on the J19 socket.  So far all I'm doing is using a small scope to check the voltages on that pin but all I see is random noise. and very low voltages, like millivolts, not the 5 volts I'm expecting.

I'm thinking I might not be setting things up properly in the Marlin firmware to access that pin properly.

What is the APPROPRIATE things I should be doing in the Firmware to successfully send text out through that TX pin?

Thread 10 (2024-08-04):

Where is AUX-2 connector on the Einsy Rambo Board?

RogerInHawaii, 2024-08-04:
Mu understanding is that there are several unused I/O pins on an AUX-2 connector, three of which are available to be configured as Interrupt pins. But I haven't come across any description of the Einsy Rambo that shows the AUX-2 connector.

So I'm hoping that someone might be able to provide a description or image or a l ink that can provide that information for me.

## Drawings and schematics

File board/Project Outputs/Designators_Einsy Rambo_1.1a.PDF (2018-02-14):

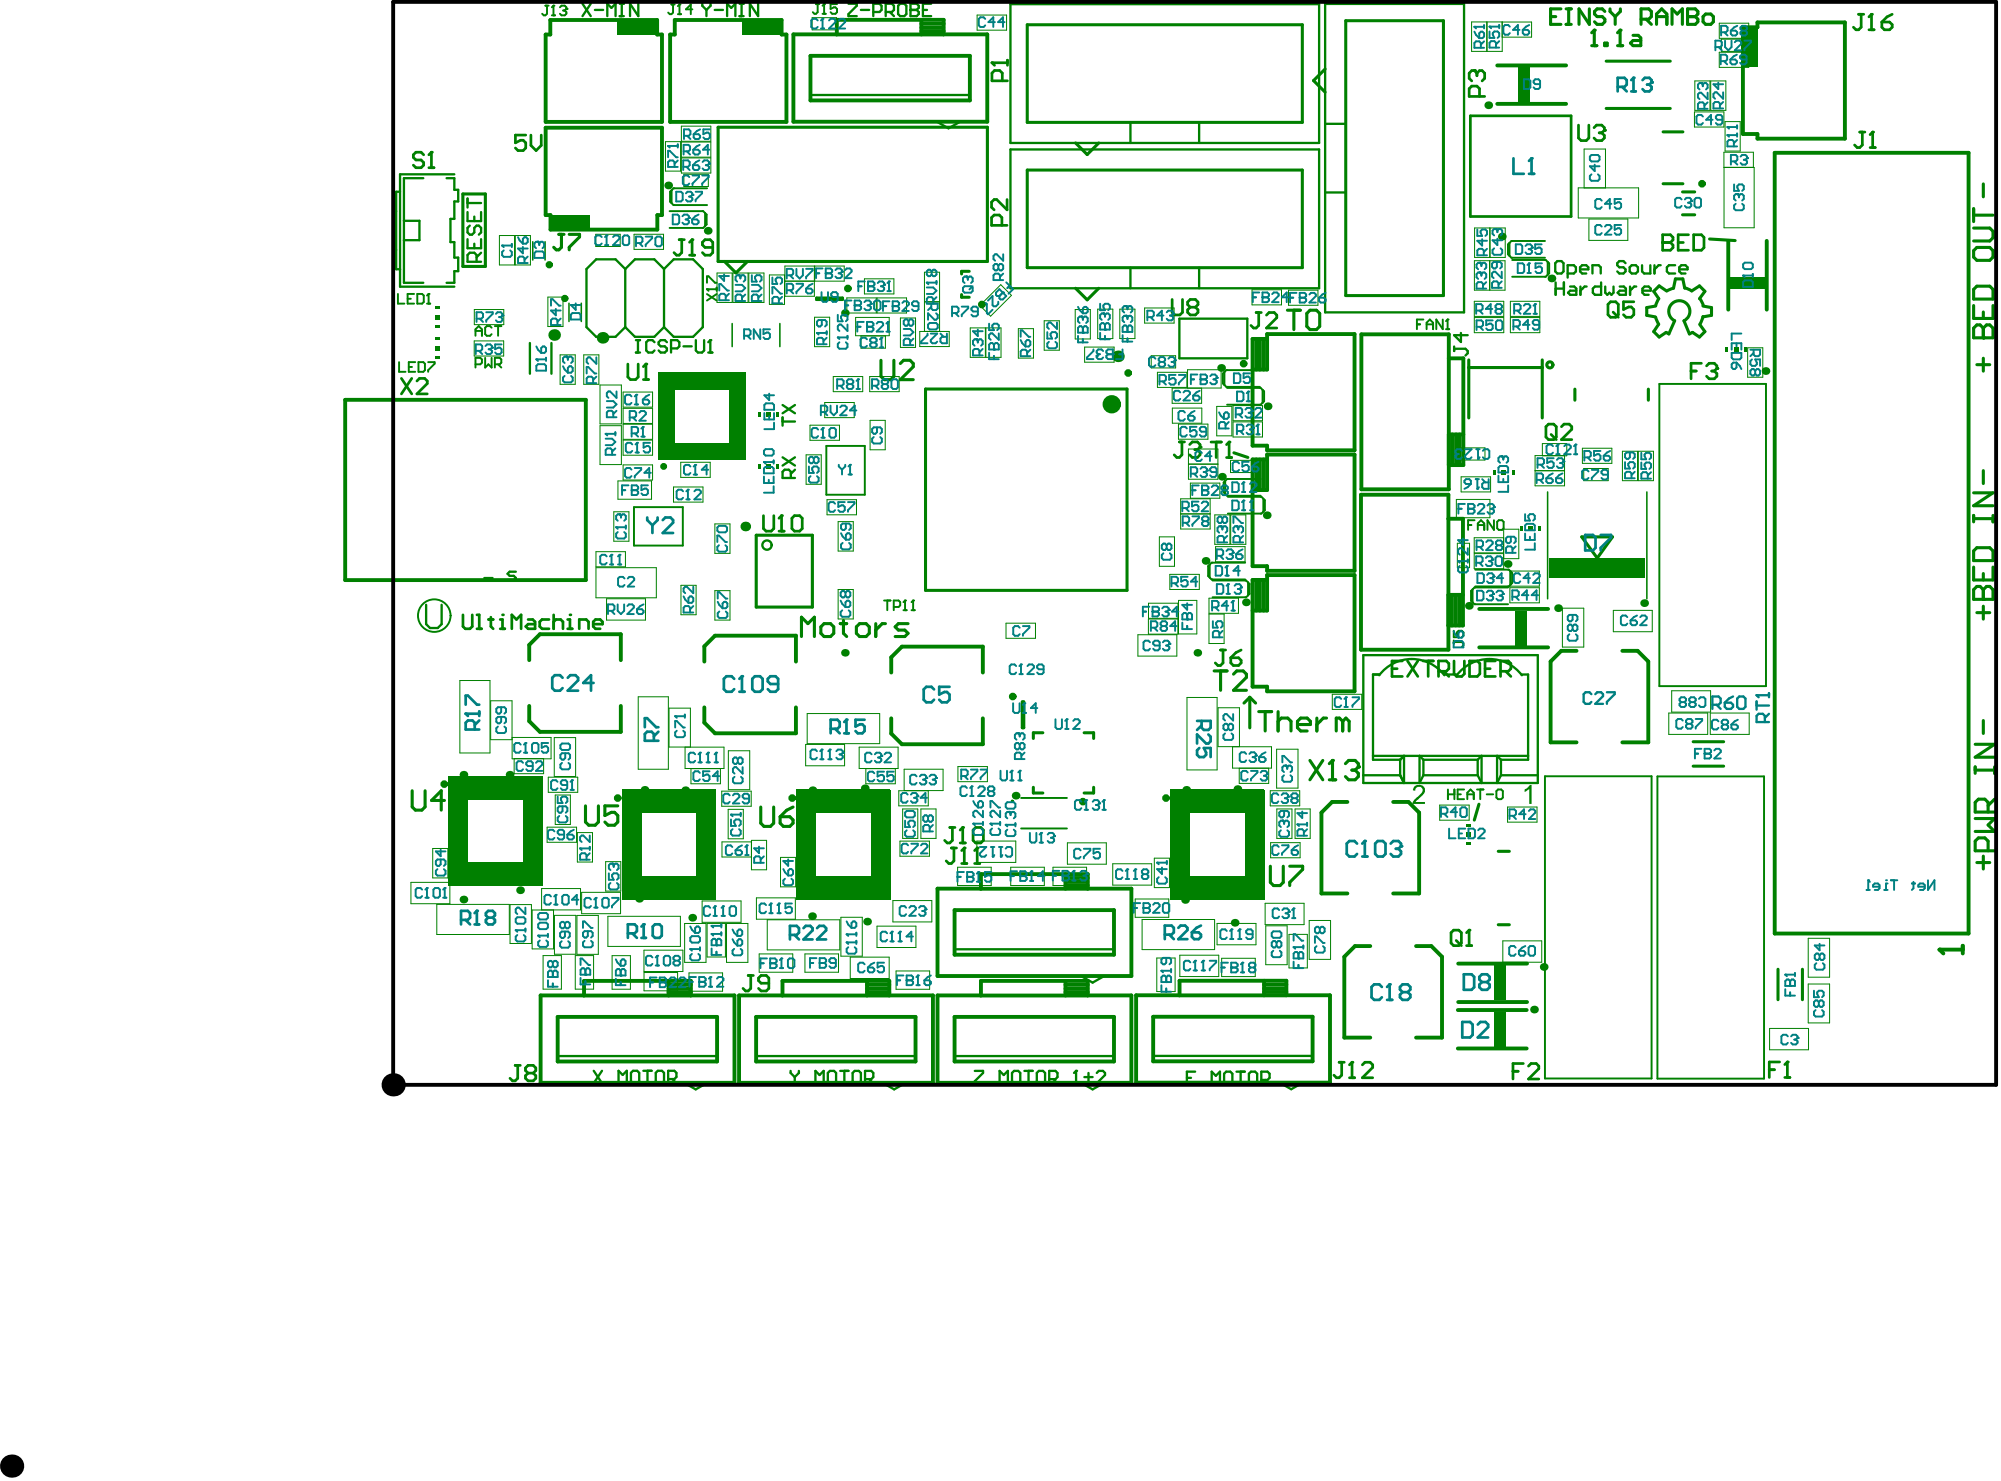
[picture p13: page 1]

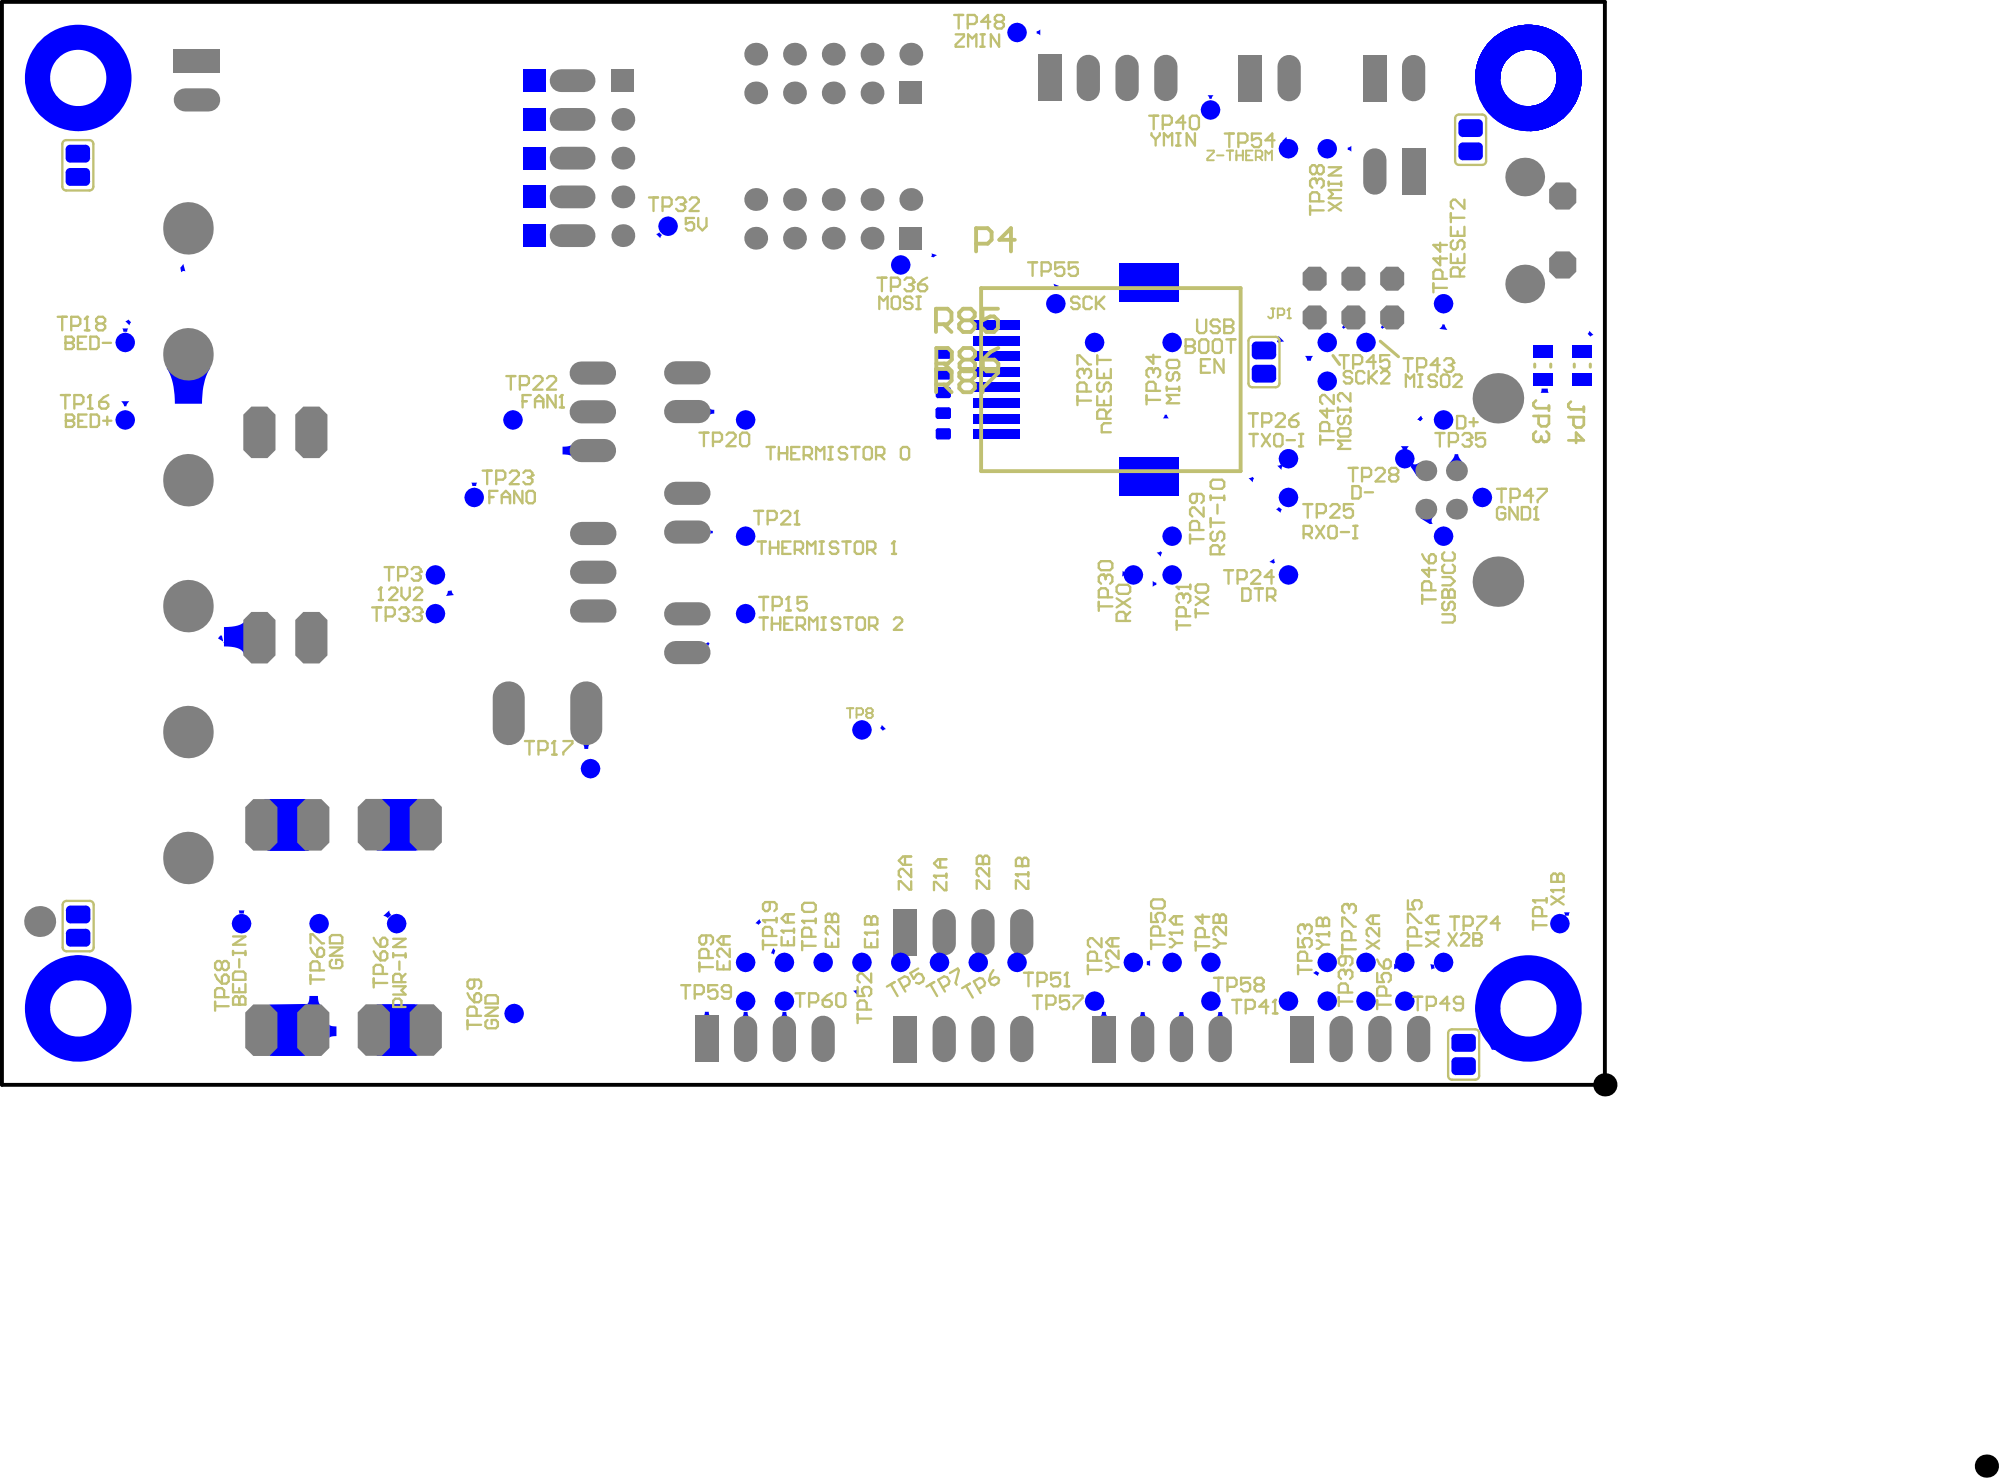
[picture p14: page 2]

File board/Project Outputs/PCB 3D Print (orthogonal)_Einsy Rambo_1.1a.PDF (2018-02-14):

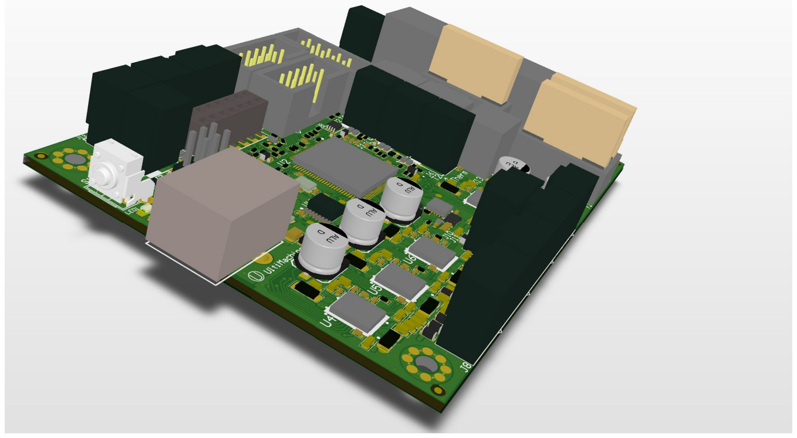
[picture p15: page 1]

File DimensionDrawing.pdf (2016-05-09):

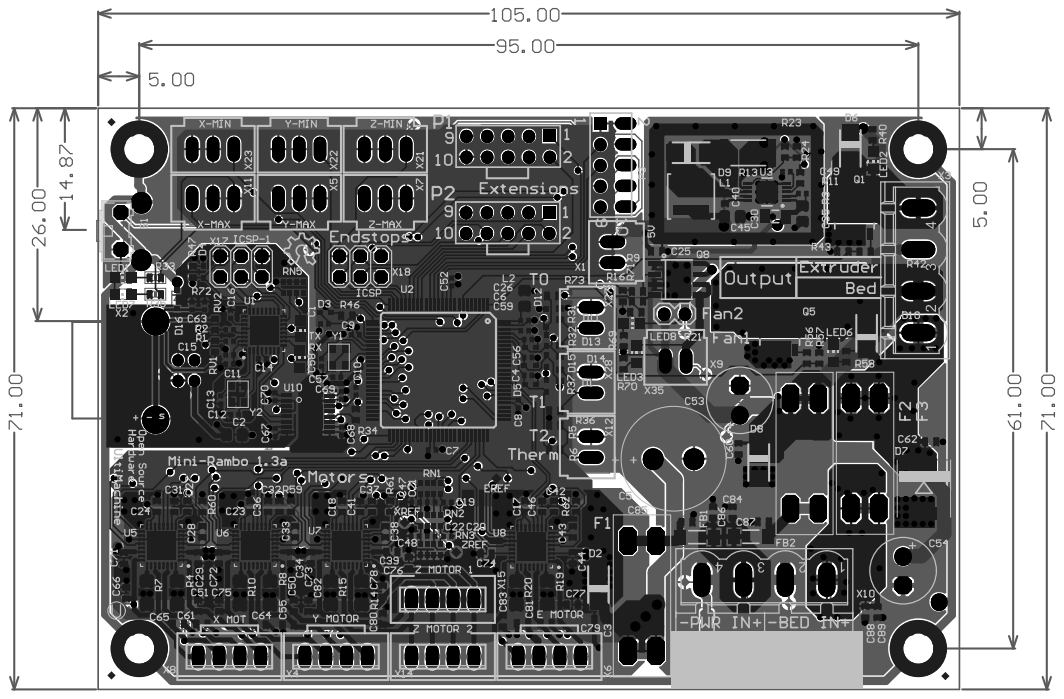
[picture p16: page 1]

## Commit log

2014-08-17 changes from prototype
    details in Project Logs
    [Heaters.SchDoc, MCU.SchDoc, Mini-Rambo-ATX.PcbDoc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]
2014-08-18 add 2x5 extension, redo SMPS layout
    [MCU.SchDoc, Mini-Rambo-ATX.PcbDoc, Mini-Rambo-ATX.PrjPcb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]
2014-08-21 remove USB fuse, remove QFP mask web, 2x5 on ATX
    [Mini-Rambo-ATX.PcbDoc, Mini-Rambo.PcbDoc, Power-ATX.SchDoc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]
2014-08-23 remove some acute angles
    [Mini-Rambo-ATX.PcbDoc, Mini-Rambo.PcbDoc]
2014-09-08 fix qfn paste and mask. rename some packages
    [Heaters.SchDoc, MCU.SchDoc, Mini-Rambo-ATX.PcbDoc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]
2014-09-15 increase clearance between fuse holder poles
    [Mini-Rambo-ATX.PcbDoc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]
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2014-10-01 add viaTent design rules, typo on diode comment
    [Mini-Rambo-ATX.PcbDoc, Mini-Rambo.PcbDoc]
2014-10-10 reduce qfn pad sizes, fix inverted paste shrink rule
    [Mini-Rambo-ATX.PcbDoc, Mini-Rambo.PcbDoc, Power-ATX.SchDoc]
2014-11-07 Rename net to E-Ref to clarify netlist
    [Mini-Rambo.PcbDoc]
2014-11-10 Change mounting holes to Rambo style
    [Heaters.SchDoc, MCU.SchDoc, Mini-Rambo.PcbDoc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]
2014-11-11 Add filter caps to motor output leads
    [Mini-Rambo.PcbDoc, Mini-Rambo.PrjPcb, Motors.SchDoc]
2014-11-11 Fix PSU inductor footprint (shrink)
    [Mini-Rambo.PcbDoc]
2014-11-12 Fix top silk
    [Mini-Rambo.PcbDoc]
2014-11-12 add motor ref test points to top
    [MCU.SchDoc, Mini-Rambo.PcbDoc]
2014-11-12 Add bottom silk, tp labels. Rename input nets
    [Heaters.SchDoc, Mini-Rambo.PcbDoc, Power-SMPS.SchDoc]
2014-11-12 top motor gnd pour over all, reroute traces from:
    0639845b946c3816577ebe621fb15a7e1ef121cd
    , regenerate gerbers
    [Mini-Rambo.GBL, Mini-Rambo.GBP, Mini-Rambo.GBS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]
2014-11-18 change voltage regulator soft start capacitor
    now 4.7nF. 1uF was too slow and could cause unstable boot of atmega
    [Mini-Rambo.PcbDoc, Mini-Rambo.PrjPcb, Power-SMPS.SchDoc]
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2014-11-28 Set testpoints not in BOM
    [Heaters.SchDoc, MCU.SchDoc, Motors.SchDoc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]
2014-12-01 Update SOT669 package to tent vias in pad
    [Mini-Rambo.PcbDoc, Mini-Rambo.PrjPcb]
2014-12-04 remove ground around mount holes, tent smps vias,
    remove test points from BOM.
    [Mini-Rambo.GBL, Mini-Rambo.GBP, Mini-Rambo.GBS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]
2015-01-06 change extension headers to 2x5 2.54mm
    [MCU.SchDoc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]
2015-02-18 Fix max endstops schematic mixup
    No change to layout/gerbers
    [MCU.SchDoc, Mini-Rambo.PcbDoc]
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2015-04-05 fuse holder > 3557-2, new fan fet, new NP caps
    [Heaters.SchDoc, Mini-Rambo.PcbDoc, Mini-Rambo.PrjPcb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]
2015-04-06 silk fixes: eMotor TP, Xdir, extension header
    [Mini-Rambo.PcbDoc]
2015-04-06 Add fuse part number to schematic
    [Mini-Rambo.PcbDoc]
2015-04-06 tweak bottom solder mask
    [Mini-Rambo.PcbDoc]
2015-04-07 Move PWR input for serial label. remove F4:
    Now have protected mosfet to limit current and failure.
    [Heaters.SchDoc, Mini-Rambo.PcbDoc, Power-SMPS.SchDoc]
2015-04-07 Via stitching for heatbed
    [Mini-Rambo.PcbDoc]
2015-04-07 Fix polygon order so usb xtal poly renders correct
    [Mini-Rambo.PcbDoc]
2015-04-11 More silk and mask tweaks
    [Heaters.SchDoc, Mini-Rambo.PcbDoc, Power-SMPS.SchDoc]
2016-04-05 Changing power connectors to barrier blocks. Add TMC2130
    [Heaters.SchDoc, Mini-Rambo.PcbDoc, Power-SMPS.SchDoc]
2016-05-09 start tmc2100 schematic and component placement
    [3delight_BOM.csv, 3delight_OriginalBOM.csv, ARROW_3delight.csv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]
2016-05-13 roughed in x and powers
    [Heaters.SchDoc, Mini-Rambo.PrjPcb, Mini-Rambo.~(90).PcbDoc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]
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2016-08-07 add missing output files
    [Einy_0.1a.GBL, Einy_0.1a.GBO, Einy_0.1a.GBP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]
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2017-03-10 0_3a changes are complete Prototype quote has been sent Schematic and BOM cleanup is yet to be done
    [Einsy_Rambo_0.3a.PrjPcb, Einsy_Rambo_0.3a_Panels.PrjPcb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]
2017-03-10 safety checkin Reworking schematic parameters Tweaked bottom layer traces to sit more tightly over the power plane
    [Connectors.SchDoc, Endstops.SchDoc, Heaters.SchDoc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]
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2017-03-15 adjusted stackup to reflect standard 4layer stackup of the board fab house Adjusted USB trace width accoring to new stackup Add 100R to the gate of all FETs
    [Connectors.SchDoc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]
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2017-03-16 Finished editing parameters for BOM generation Cleaned up old files
    [Connectors.SchDoc, Einsy-Rambo-0.3a BOM-Grouped 20170316.xlsx, Einsy-Rambo-0.3a BOM-Single 20170316.xlsx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]
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2017-06-08 all known changes complete Added prelim schematics for Prusa About to move designators to a mechanical layer
    [Connectors.SchDoc, Endstops.SchDoc, Heaters.SchDoc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]
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2017-06-14 All changes made for 0_4a Clean DRC on PCB
    [Connectors.SchDoc, Einsy_Rambo_0.4a.PrjPcb, Endstops.SchDoc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]
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2017-07-08 Replace Arduino pin numbers in schematic
    [MCU.SchDoc]
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2017-07-27 adding ferrites to display headers Ferrites added to motor outputs
    [Connectors.SchDoc, Einsy_Rambo_0.5a.PrjPcb, MCU.SchDoc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]
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2017-07-28 replace F1 circuit, polygon tweaks
    [Einsy_Rambo_0.5a.PrjPcb, Endstops.SchDoc, Motor-E.SchDoc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]
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2017-07-28 internal layers polygon clearance 12mil, new 0.5a gerbers
    [Einsy_Rambo_Panel.xls, Pick Place for Einsy_Rambo_Panel.csv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]
2017-07-28 Updating info for new parts Listing changes on title page Publishing board support documents
    [Connectors.SchDoc, Einsy Rambo 0.5a GROUPED 20170728.ods, Einsy Rambo 0.5a UNGROUPED 20170728.ods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]
2017-07-28 Schematic and PCB doc are now synced NO PHYSICAL CHANGES TO PCB SINCE CHECKIN f8d40d9
    [Einsy_Rambo_0.5a.PrjPcb]
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2017-08-01 C88 and 89 are no longer DNI
    [Einsy Rambo 0.5a GROUPED 20170728.ods, Einsy Rambo 0.5a GROUPED 20170801.ods, Einsy Rambo 0.5a UNGROUPED 20170728.ods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]
2017-08-05 Updated PCB Panels need to be updated and files generated
    [Einsy_Rambo_0.5a.PrjPcb, Heaters.SchDoc, MCU.SchDoc]
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2017-08-08 add board thermistor, 32u2 power jumpers, change thieving and planes a bit
    [Einsy_Rambo_0.5a.PrjPcb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]
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2017-09-28 move vias out of fuseholder solders, solder jumper default each mount hole to gnd, gen 1.0a outputs
    [Einsy_Rambo.PrjPcb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]
2017-10-17 New schematic template applied All sheets are now Letter sized Updated version changes for 1_0a on title page
    [Connectors.SchDoc, Einsy_Rambo.PrjPcb, Einsy_Rambo_0.5a_Panels.PrjPcb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]
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2017-11-12 add RPI reset transistor schem
    [Connectors.SchDoc]
2017-11-13 layout buffer and reset patches
    [Connectors.SchDoc, Einsy_Rambo.PrjPcb]
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2017-11-14 Finished thermal via barrel relief Generated 1up and panel files
    [25543_csident.gbr, 25543_csmask.gbr, 25543_cspaste.gbr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]
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2017-11-21 add resistors and ground to bottom serial conn
    [Connectors.SchDoc]
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2018-02-14 regenerate 1.1a pdfs for connector changes already in source
    [Einsy_Rambo.PrjPcb]
2018-05-03 Populated some TBD components Updated parameters on RJ45 connector
    [BOM-Grouped_Einsy Rambo_1.1a.xls, Connectors.SchDoc, Pick and Place_Einsy Rambo_1.1a.csv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]
2018-05-03 Added PinInPaste to select connectors Generated gerbers for top and bottom paste
    [Connectors.SchDoc, Einsy_Rambo.PrjPcb, Endstops.SchDoc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]
2018-05-07 fix rj45 footprint
    [Einsy_Rambo_Panel.GBL, Einsy_Rambo_Panel.GBO, Einsy_Rambo_Panel.GBP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]
